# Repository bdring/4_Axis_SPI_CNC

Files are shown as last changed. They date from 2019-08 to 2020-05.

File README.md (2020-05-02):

# A 4 axis ESP32 CNC controller for daisy chained SPI stepper drivers.

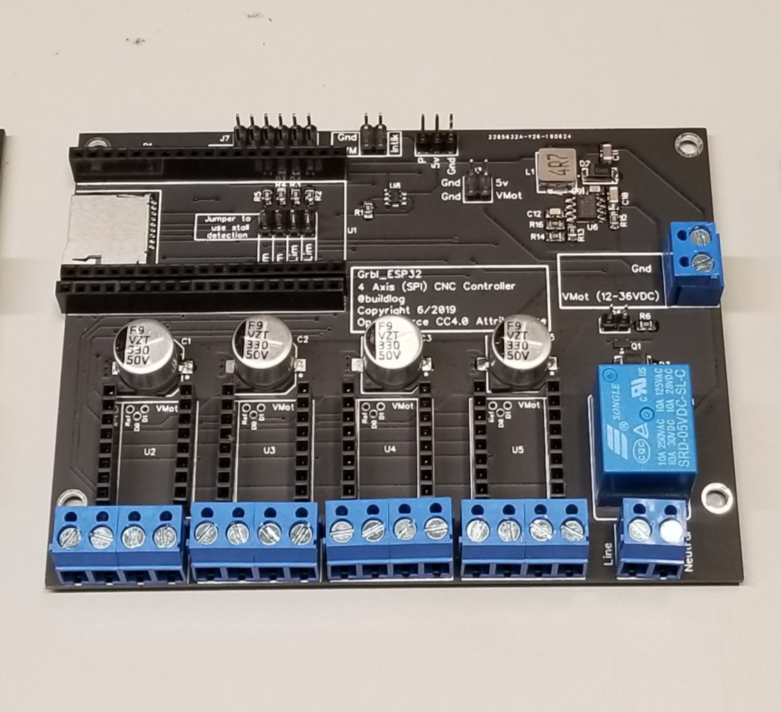
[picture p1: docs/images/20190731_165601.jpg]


### Trinamic Drivers

[Trinamic SPI stepper motor drivers](https://www.trinamic.com/products/integrated-circuits/) are great. They have dozens of features not found on traditional small stepper drivers. You can't control all the features via configuration pins, like the MS1, MS2 and MS3 traditionally used to select microstepping. They use SPI to setup and control the features. 

**Note:** Some of these drivers are sold in a pre-configured mode. They are often call "Stand Alone" versions of the drivers. This project is not compatible with those. It only works with SPI controlled drivers.

### About SPI Daisy Chaining

Typically each SPI device requires a SS (slave select) signal. With multiple drivers, this can cause problems with I/O pin count limited controllers, like the ESP32.

Most SPI devices can be used in a daisy chain mode (see image). As bits are received into a register via the MOSI pin,  bits are shifted out of the register of the MISO pin. Trinamic drivers use a a 40 bit wide register. To write to all three drivers shown below, you would send (3) sets of 40 bits. The first set of 40 bits would end up in the last driver. The SS line is pulled low once all drivers have their data. To write to only one driver, dummy data would be sent to the non targeted drivers. 



There is a very comprehensive and easy to use library, [TMCStepper](https://github.com/teemuatlut/TMCStepper), for SPI control, but it does not support daisy chaining. I created a fork that has a basic ability to write to any driver in an SPI daisy chain. It does not support reading data yet.

### Notes about the controller

- The SD card and drivers share the same SPI data lines. There is one SS for the SD and one SS for all of the drivers. 
- If you use less than (4) drivers, you need to jumper MOSI to MISO on the missing drivers to close the daisy chain loop.
- You can connect the DIAG1 pin of the drivers to the limit switches using jumpers JP1-JP4. Be sure to remove only one type of limit switch at a time.
- Source files
  - [Schematic (PDF)](https://github.com/bdring/4_Axis_SPI_CNC/blob/master/docs/1p3/SPI_4Axis_V1p3_Schm.pdf)
  - [Source Files (DipTrace)](https://github.com/bdring/4_Axis_SPI_CNC/tree/master/source/1p3/DipTrace)
  - [Gerbers](https://github.com/bdring/4_Axis_SPI_CNC/tree/master/source/1p3/Gerber)
  
### Plug In Modules

 - ESP32: The PCB uses ESP32 Dev Modules. It uses the 2 x 19 pin types with pin widths of either 0.9" or 1.0". 
 - Motor Drivers: It uses stepstick style stepper motor drivers with Trinamic SPI drivers. It has extra large capacitors.

### Firmware

- Use [Grbl_ESP32](https://github.com/bdring/Grbl_Esp32) with [spi_daisy_4axis.h](https://github.com/bdring/Grbl_Esp32/blob/master/Grbl_Esp32/Machines/spi_daisy_4axis.h) machine file

### I/O Expanders

Note: Obviously, external I/O expanders can be used increase I/O pin count. This project is focused on using only the I/O on the ESP32.

### Revision History

- **V1p2**
  - Added bypass jumper for 4th axis. Install jumper if 4th axis is not used. Normally the daisy chained SPI has to go through that axis.
  - Added 10uF optional capacitor to help with ESP32 modules that have trouble entering bootloader mode. This is not installed by default.
  - Added extra ground connection that TMC5160 drivers need. It is N/C on many other TMC drivers.

### Donation

This project represents a lot of work. Please consider a safe, secure and highly appreciated donation via the PayPal link below.



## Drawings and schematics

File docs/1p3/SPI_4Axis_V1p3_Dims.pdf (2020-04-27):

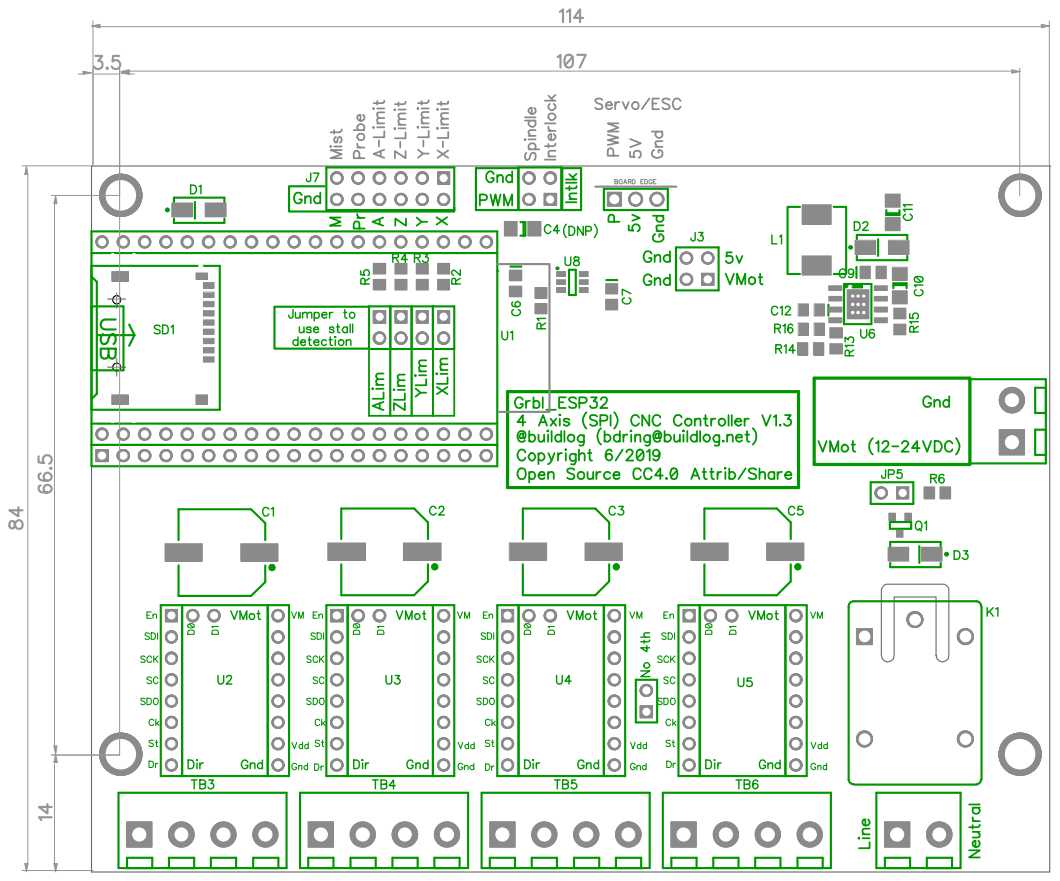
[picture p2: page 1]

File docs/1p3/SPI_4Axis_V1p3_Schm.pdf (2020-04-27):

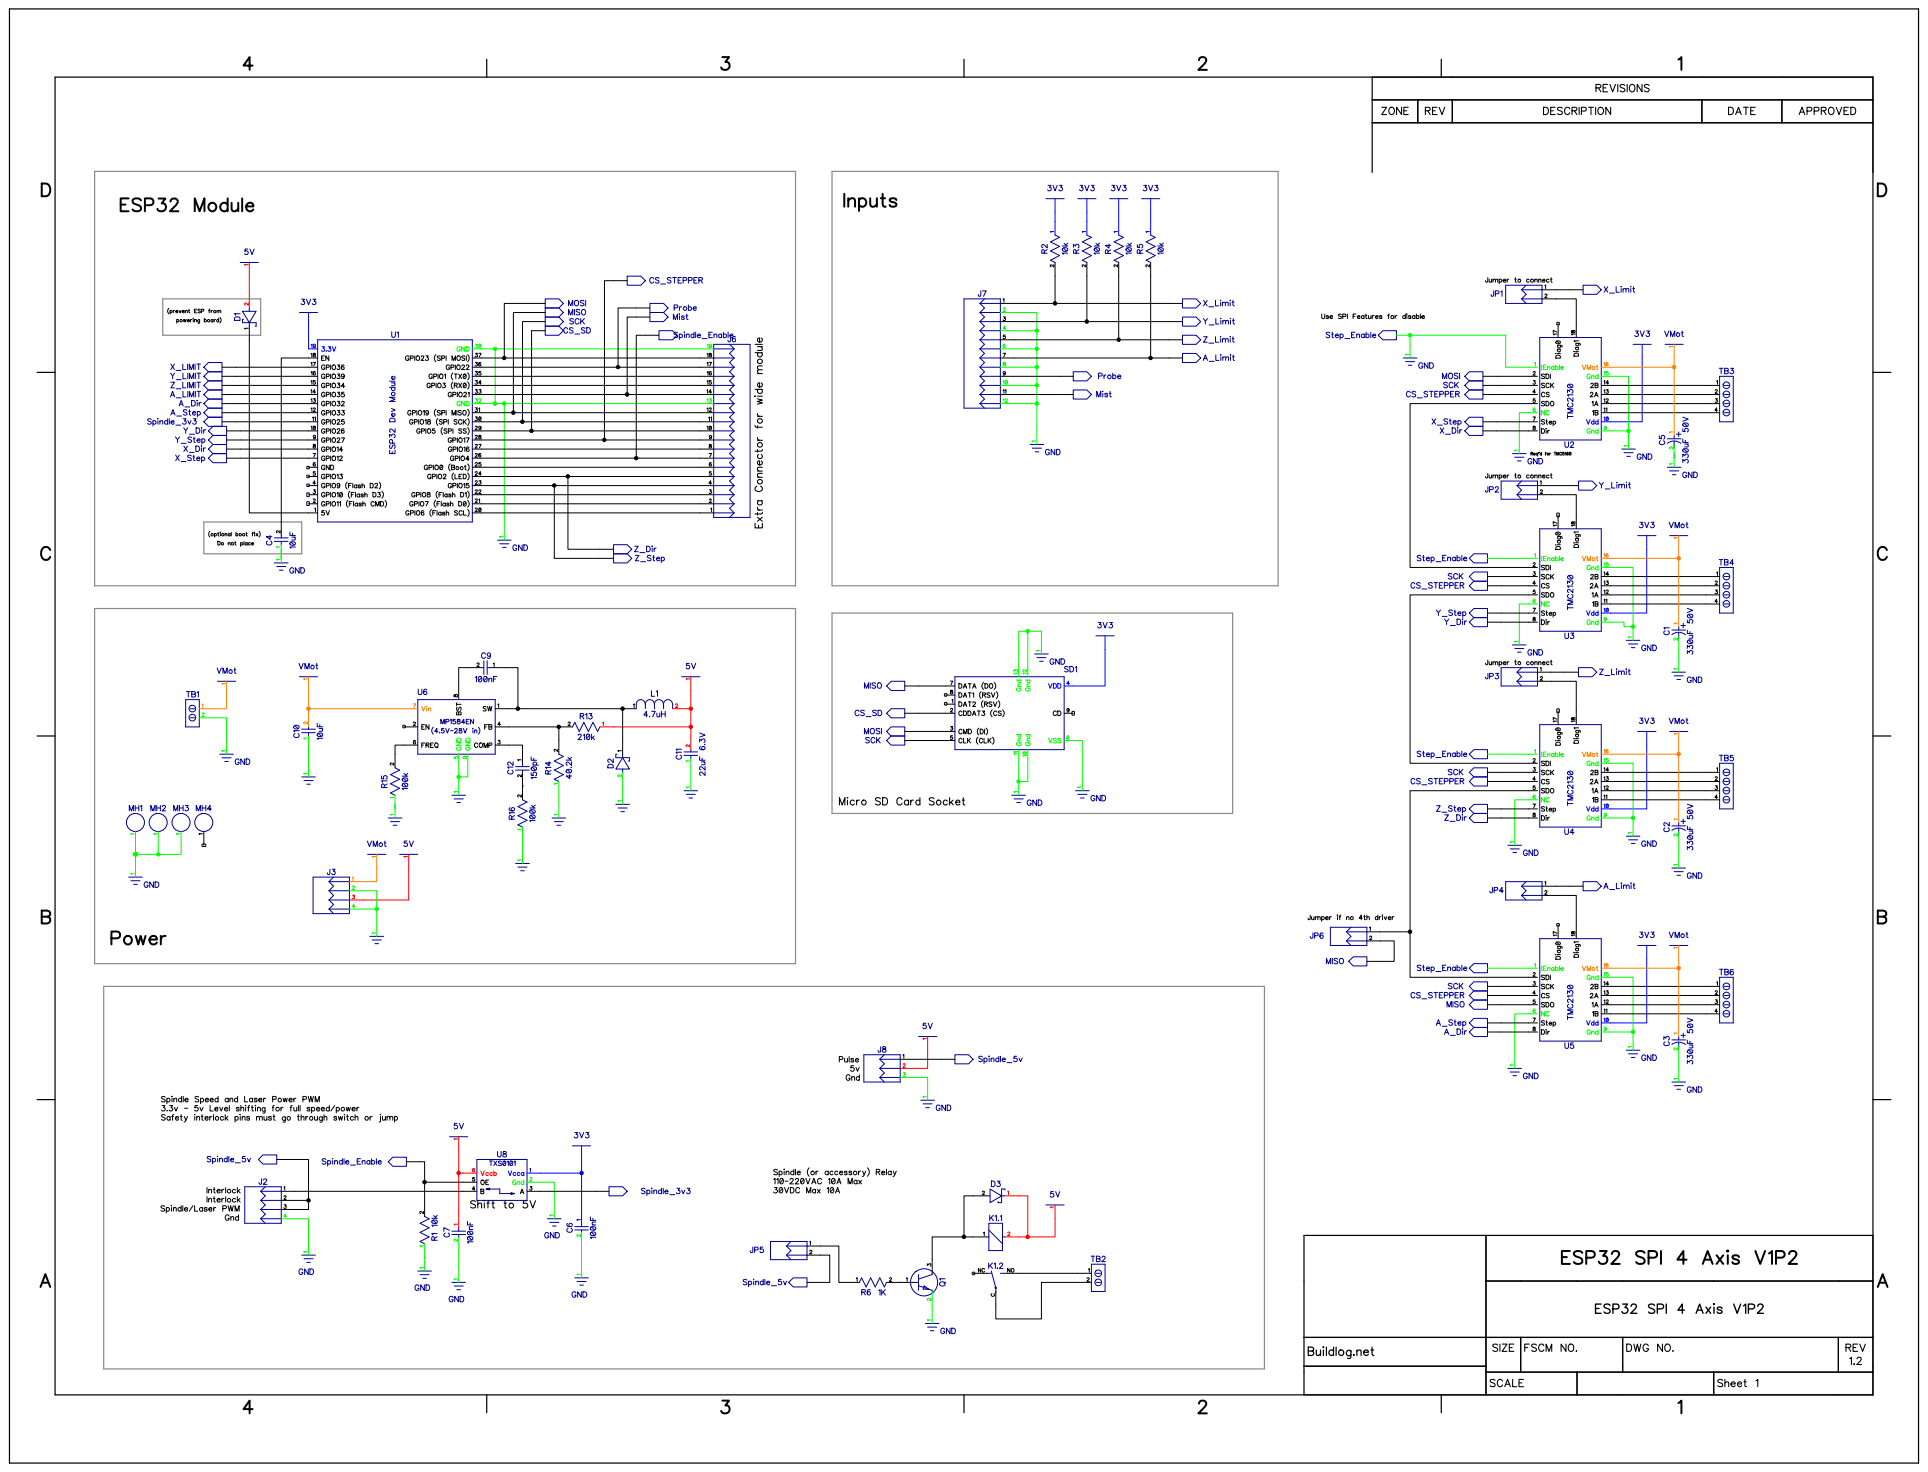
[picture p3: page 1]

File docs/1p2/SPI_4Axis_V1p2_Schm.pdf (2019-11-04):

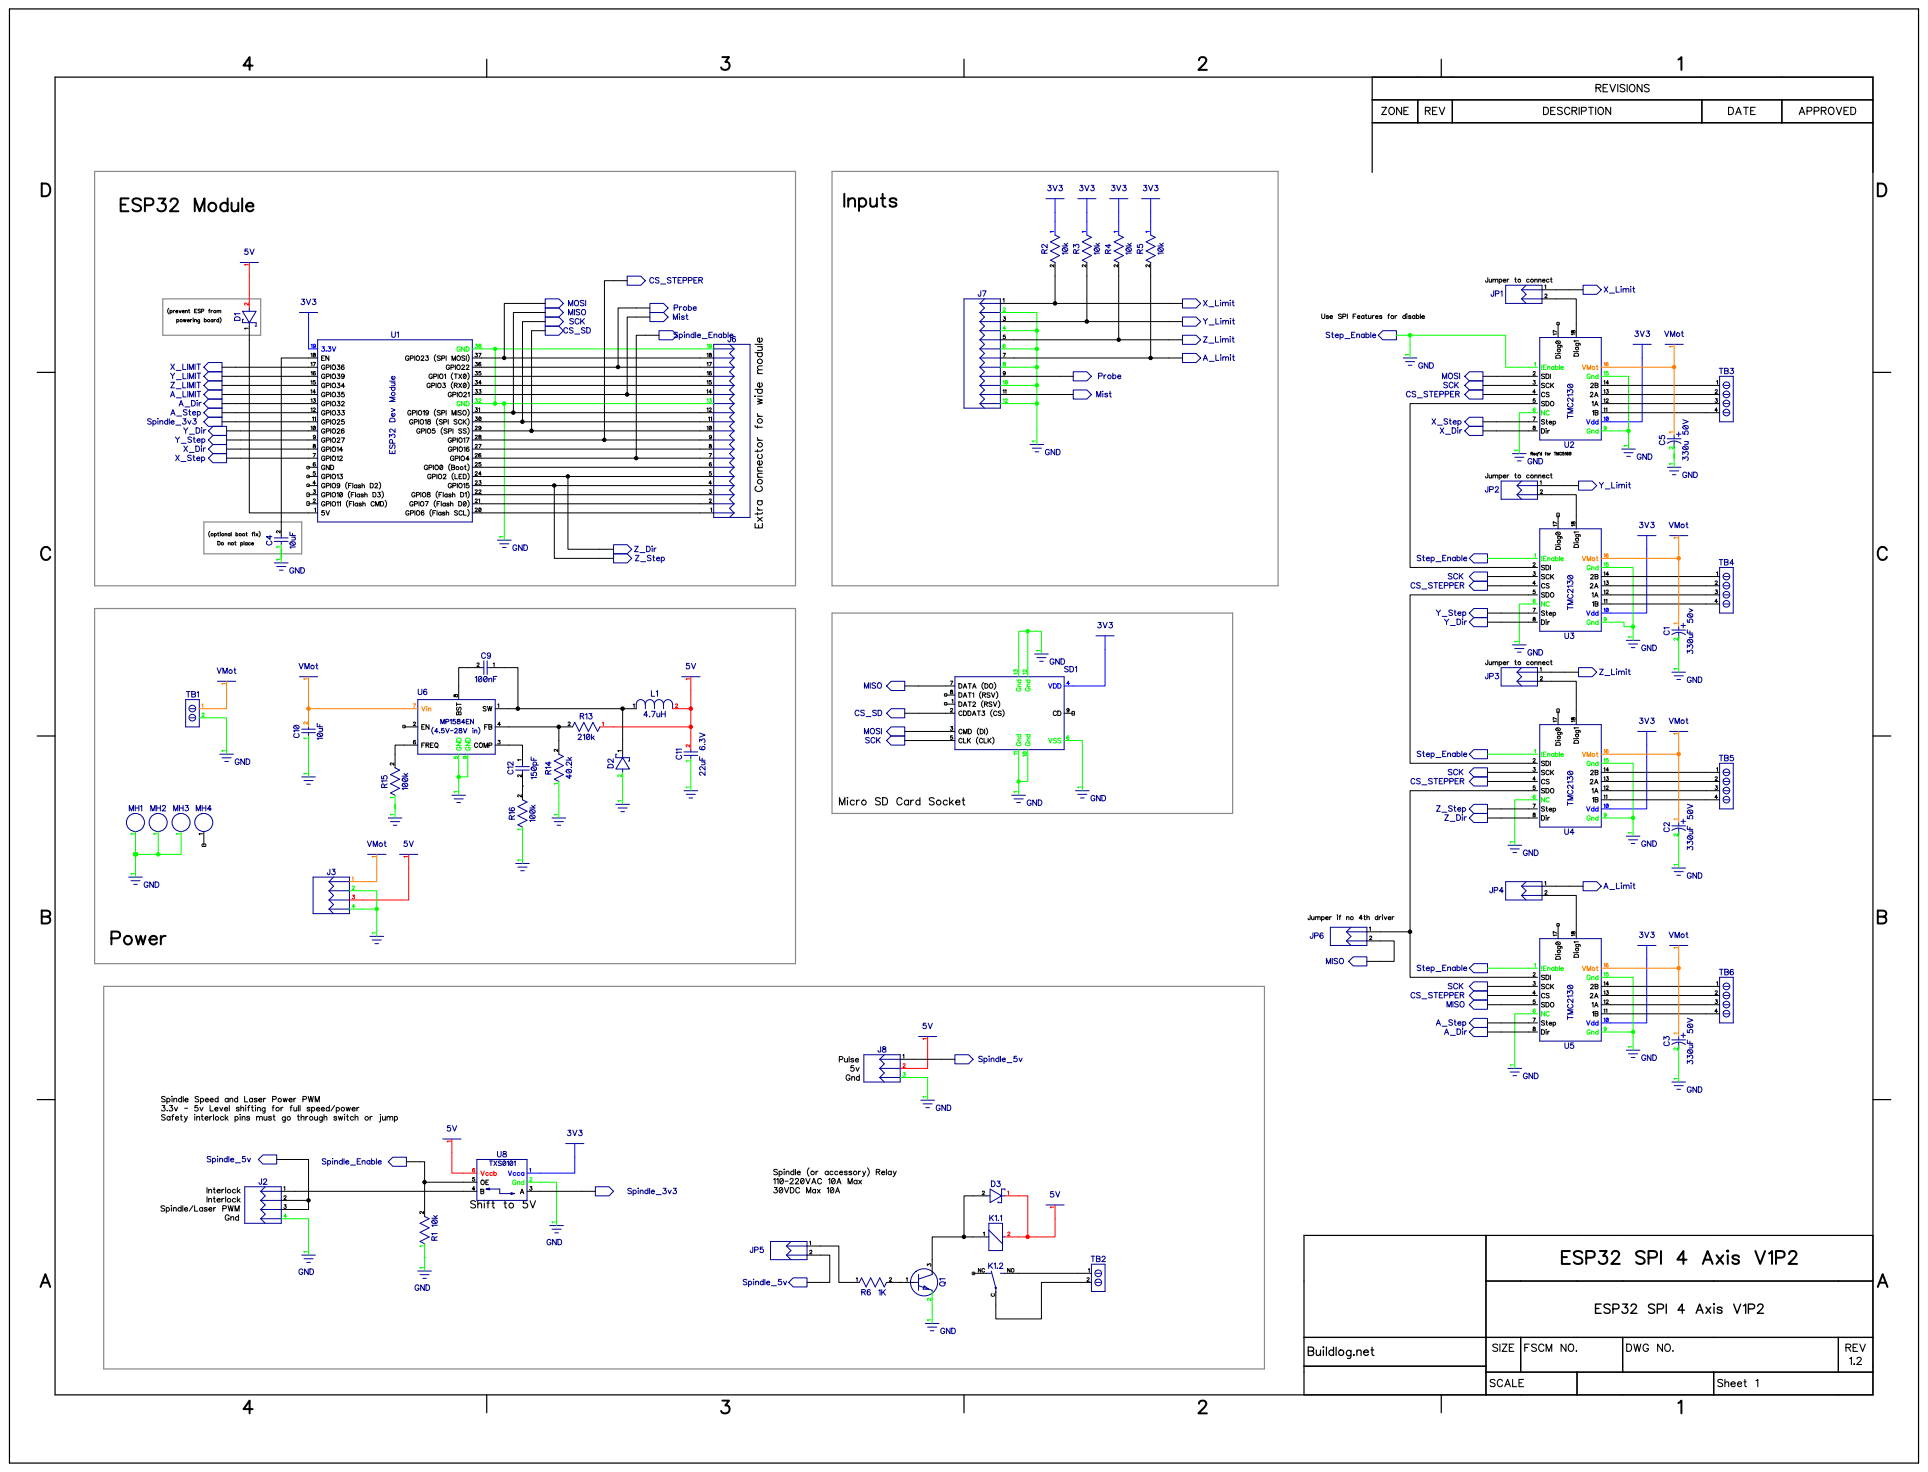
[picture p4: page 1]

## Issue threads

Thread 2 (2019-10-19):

where is cpu_map.h ?

cxandy, 2019-10-19:
thanks.

bdring, 2019-10-19:
This board used to require a fork of Grbl_ESP32 and a fork of TMCStepper.

The original TMCStepper has been updated to support daisy chained SPI and Grbl_ESP32 now uses that version. The old fork of Grbl_ESP32 was removed.

Support for daisy chained SPI can now be added to the master branch, but it has not been done yet. It is on my todo list, but behind a few other priorities. I hope to have it done by the end of the month.

shreeramlive, 2019-11-04:
In the schematic I noticed that the **Step/Dir** pins are physically connected to the ESP32 board. Do we need them for **SPI connection**, if they are not needed we can add some switches like Hold, Resume.
And the connection to the limit switches are without any **filter capacitors** unlike the [Grbl_ESP32](https://github.com/bdring/Grbl_ESP32_Development_Controller/blob/master/source/V3p5/schematic_esp32_cnc_test_v3p5.pdf) development board, are they necessary for the ESP32 boards?

bdring, 2019-11-04:
**Step/Dir** They are required. SPI primarily sets the features of the driver. It does have the ability to run motion profiles, but not step and direction. You could eliminate the driver **enable** pin. All the drivers share this one pin, but support would need to be added to Grbl for it.

**R/C filters on inputs** It is not typically required for smaller machines. Grbl also has debouncing that can be used. If you are using a larger machine with a high current spindle or laser, you might want to use them.

shreeramlive, 2019-11-09:
Hi, I have created a schematic with a slightly different pin map. **RC filters** are added for limit switches to be able to use with large machines.

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

[Schematic_esp32 grblcnc bk_Sheet_1 edit copy_20191109121537.pdf](https://github.com/bdring/4_Axis_SPI_CNC/files/3826991/Schematic_esp32.grblcnc.bk_Sheet_1.edit.copy_20191109121537.pdf)

A **TXS0104 level shifter** is also added to provide four 5V output pins to drive servo axes and spindle.
When spindle enable and coolant is not needed, can we use the `level shifter` pins as **inputs** for other functions like hold, resume?

I'm trying to create a prototype with this design, Do I have change any pin configuration?
Thanks

bdring, 2019-11-09:
As drawn, those are not R/C filters. There is no "R".

I suggest grounding the CLK pin on the drivers to make it compatible with TMC5160

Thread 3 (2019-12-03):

Connection issue with daisy chained TMC5160's

shreeramlive, 2019-12-03:
Hi I tried to connect 4 **TMC5160** in daisy chain. However I could not get the motor moving.  There seems to be a **SPI problem** with the TMC5160s. I have also _grounded_ the CLK pin

However I'm pretty sure that the boards works because when I connected the` A4988 drivers `it was working perfectly.
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
Here's the ESP32 connection diagram.

Is there any way to debug the TMC connection like in marlin (**M122**)?
I think there is a problem with the TMC5160 drivers, a fix for SKR1.3 was provided [here](https://github.com/teemuatlut/TMCStepper/pull/63/commits/c481cccf542f3243c2c0594f5cf765fde2dd22d0)
This was a patch for the SKR1.3 (LPC1768), Is there anything similar to get it working with the ESP32.
Thank you

BTW: This board is designed to support both standalone drivers and SPI drivers. That's how I was able to test the A4988 drivers

shreeramlive, 2019-12-03:
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

Here are some photos, Everything works well except the TMC5160 SPI connection.
P.S: Board named after the project creator @bdring.

bdring, 2019-12-03:
Can you provide the complete schematic, or at least the TMC5160 connections?

shreeramlive, 2019-12-03:
Yeah sure,
Most of the connections are similar to your 4 axis SPI board.

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

The extra headers are allow us to configure SD and SPI connections
Since I'm using TMC5160, I have grounded the CLK to ground

[sch2.0.pdf](https://github.com/bdring/4_Axis_SPI_CNC/files/3917623/sch2.0.pdf)

bdring, 2019-12-03:
What is the purpose of the stepper headers connected to 3.3V and CLK?

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

Try connecting CLK to ground.

shreeramlive, 2019-12-17:
**Thanks @bdring**, I have tried connecting the **CLK to ground**. Nevermind the headers in the schematic. Those extra headers are used to configure **Microsteps or SPI** connections with the help of **jumpers.**

Still no success with the TMC5160 stepsticks, I'm kind of confident that the _issue is with the TMC5160 drivers_. I have ordered some `TMC2130's` for testing. I will post updates when I receive them.

Is there any way to **debug** the `SPI connection` with the drivers?

Baramykin, 2020-12-24:
Hi,
I don't understand how to connect TMC5160 8 pcs to Teensy 4.1 in UART mode.
I can't find the schematics.
I want to use TMC5160 V1.2 drivers.
Help me if possible, please.

creatormir, 2021-05-11:
I've come to see the serial connection.
And about the SPI, I think the problem is the StepStick board. The SPI is blocked. We need to cut the track. That's where the https://github.com/bigtreetech/BIGTREETECH-TMC5160-V1.0/issues/8 discussed it.

The place to cut. It helped me.
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

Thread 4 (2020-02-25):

where to buy

haklein, 2020-02-25:
Hi @bdring,

would it be possible to buy one of the testing boards? I've some experience with TMCs from my Powder'o'matic project (https://github.com/haklein/Powder-O-Matic). I'd like to help with testing and convert a CNC controller (from an RS-CNC32) with external drivers to TMC5160.

br Hari

bdring, 2020-02-25:
I have a new version 1.3 that I plan to sell on Tindie soon. It will probably be at least 4-5 weeks before they are ready due to the problems in China.

I have 3 hand built prototypes that I would be happy to sell for $60 each. They would not include drivers or ESP32.

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

haklein, 2020-02-25:
I'd happily take one of these prototypes (I'd assume all features are tested and it's the same as the final version?).

bdring, 2020-02-25:
The design is 100% tested. Also, some new features have been added to Grbl_ESP32 to allow any these axes to be combined (2 motor on one axis).

Please sent $60 + $5 US shipping or $14 International to the PayPal donation link on the first page of this repo. Be sure to add a note about reason for the donation and include the shipping address. It will ship before the end of the week.

PolSerg, 2020-02-25:
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

Hello! And what is the difference from version 1.2, were there errors? I have already made a 1.2 board for myself, but have not yet soldered it, do I need to fix something to make it work?

bdring, 2020-02-25:
There is very little change between 1.2 and 1.3. 1.2 should work fine. These days there is very little additional cost to making changes between orders.

I think the input voltage range is mis-labeled on the 1.2. Max voltage should be 24VDC. The limiting factor for the input voltage is the 5V power supply.

haklein, 2020-02-28:
@bdring do I need a special branch of Grbl_ESP32 to run this board with TMC5160 and SPI? Or has this been integrated in master?

haklein, 2020-02-28:
pls ignore my last comment, I found  CPU_MAP_SPI_DAISY_4X in the map on master

haklein, 2020-03-25:
I'm very impressed with your board. Also with your code. Thanks a lot! The steppers work fine on my 3 axes, but I'm unable to trigger the relay. The interlock jumper is set (connecting the both interlock pins). The JP5 close to the relay is also bridged.
One of the Relay pins seems to not be soldered. Is this intentional?

bdring, 2020-03-25:
All pins should be soldered.

Your settings are correct.

haklein, 2020-03-25:
I've soldered the pin but the relay is still not working. I've verified GPIO 25 (Spindle_3v3) with a multimeter, and it toggles from 0 to 3.3V when being turned on via M3. But that's not arriving as 5V signal at the interlock.

haklein, 2020-03-25:
Applying 5V to JP5 operates the relay, so apparently there is an issue with the TXS0101. From the datasheets, the voltages at the pins should be fine. But I'm unsure about the orientation of the package, mind to cross check?
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

bdring, 2020-03-25:
That orientation is correct. do you have both jumpers installed?

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

haklein, 2020-03-25:
Yes, I have both jumpers connected as shown in your picture. I just had removed the interlock when taking the picture as I was also measuring on those pins.

bdring, 2020-03-26:
Remove the jumpers and measure the voltage with spindle on at GPIO_NUM_25, GPIO_NUM_4 and the  inner side of the interlock jumper.

haklein, 2020-03-26:
With both jumpers removed, when spindle is on, I get the following readings:
G25: 3,18V
G4: 3,17V
Inner side (closer to C4 pad) Interlock: 0,002V

bdring, 2020-03-26:
Measure the the voltage on the J3 5V pin.

On Thu, Mar 26, 2020 at 10:23 AM Harald Klein <notifications@github.com>
wrote:

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

--
Bart Dring

"If you did not build it, you will never own it"

haklein, 2020-03-26:
J3 5V shows 4,95V

bdring, 2020-03-26:
It seems like the level shifter is not working.  If you are just using the spindle, you could try to bypass the level shifter. The relay will work on 3.3V.

haklein, 2020-03-26:
Ok, thanks for the hint, I will try that. Can you tell me the exact part number for the shifter (same package/footprint etc), then I'll attempt to replace it.

bdring, 2020-03-26:
Texas Instriments TXS0101

haklein, 2020-03-26:
the TXS0101DBV as SOT-23 (6)?

bdring, 2020-03-26:
Yes.

If you want to bypass it, just remove it and bridge these 2 pins.

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

haklein, 2020-03-27:
I've connected GPIO25 to the right pin of JP5 with a wire, relay works with G3/G5 now. That will do fine until the TXS0101DBV arrives. Thanks for the hint.

haklein, 2020-04-16:
The replacement TXS0101DBV did arrive today. After replacement, the relay did still not work. In the end it was the solder joints of R1, apparently one was cold. Re-heating made the relay work. Thanks for your support and the nice board.

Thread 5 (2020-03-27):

[RFE] serial header

haklein, 2020-03-27:
It would be nice to have the serial pins accessible on a 4-pin header (RX, TX, GND, 5V). That would allow to easily connect a controller like: https://github.com/mstrens/grbl_controller_esp32

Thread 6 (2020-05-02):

Schematics link broken

VincentFrangi, 2020-05-02:
Hello,

The link to the schematics.pdf and some other links of README.md file are broke.
Thank you

bdring, 2020-05-02:
Thanks...fixed

Closed 2020-05-02.

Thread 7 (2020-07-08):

BOM anywhere?

gitxmax, 2020-07-08:
I'm far from US, so ordering the pre-made board is next to impossible.
Uploaded the gerber to Jlcpcb and found they can do SMT.
The problem is I went through every corner of this repository but failed to find the components list.
Any hint?
Thank you!

bdring, 2020-07-08:
Here is a PDF.

Note: JLCPCB has a very restrictive list of parts. I have never been able to use their service.

[SPI_4X V1.3 BOM.pdf](https://github.com/bdring/4_Axis_SPI_CNC/files/4892292/SPI_4X.V1.3.BOM.pdf)

gitxmax, 2020-07-10:
Thank you.
Went throgh the BOM, seems the following 2 components, might be a bit hard to get for me:

TXS0101DBVR - Level shifter
MMBT9013H - Transistor

Can this be replaced with something similar?

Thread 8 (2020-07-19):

Will this work with the TMC2208 V3

DrJohnM61, 2020-07-19:
First I just wanted to say that this is a fantastic initiative. I am about to purchase.

The spi_daisy_4axis.h file does not exist. Should I just use spi_daisy_4axis_xyz.h?

I notice that the Grbl_ESP32 code supports TMC2130, TMC2209 and TMC5160. I happen to have a number of TMC2208v3 spare and wonder if they can also be used? Apart from max current output and senseless homing (which I do not think you use anyway) and heat output, the TMC2209 and 2208 should be interoperable?

However, grbl_trinamic.h only defines TMC2130_RSENSE_DEFAULT and TMC5160_RSENSE_DEFAULT (and not for the TMC2209). Is that an omission? The TMC2209 (and 08) have the same as the TMC2130 ( 0.11). Should I update grbl_trinamic.h to include (at least) a TMC2209 and update spi_daisy_4axis_xyz.h to reflect the use of the different stepper?

Further, I get a warning on compiling stating "WARNING: library TMCStepper claims to run on avr architecture(s) and may be incompatible with your current board which runs on esp32 architecture(s)." - is this an issue or do I have to set some switch in the code to ensure compatibility?

Thank you in advance

DrJohnM61, 2020-08-20:
I went with TMC2130 so this is a non issue now.

Closed 2020-08-20.

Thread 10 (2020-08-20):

SD card not recognised

DrJohnM61, 2020-08-20:
I have tried plugging in an SD card (128mb) and tried a number of different formats (FAT12 and FAT), however, the ESP_32 web interface reports that there is no SD card. Is there a trick to getting the SD card to be recognised (I checked the code and the SD card option is tuned on). Does there are need to be in some other format (eg EXT)?

DrJohnM61, 2020-08-20:
By way of an update, the actual message in the web interface is "No SD Card". I also just tried the sd card formatted as ext4 without any joy.

bdring, 2020-08-20:
The wiki has some suggestions.

https://github.com/bdring/Grbl_Esp32/wiki/Using-the-SD-Card#card-formatting

DrJohnM61, 2020-08-20:
> The wiki has some suggestions.
>
> https://github.com/bdring/Grbl_Esp32/wiki/Using-the-SD-Card#card-formatting

Thank for directing me to that page. I am running on a Mac and also Raspberry pi, so that formatting solution did not work. I swapped out the card for a different one and that is recognised. On the basis that the no-working card is 128mb (yes mb, not gb), I suspect that it may be that the ESP-32 just does not like the card that is probably quite old.

Anyway - seems like I have a solution... Thanks for your help.

Closed 2020-08-20.

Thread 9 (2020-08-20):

Z Probe

DrJohnM61, 2020-08-20:
I have connected a basic touch contact to the probe connector but this does not work. I notice that the X/Y/Z/A limit switches have a 10k pull up resistor. Is this also required (to be added) for the probe pins or do I need some other type of probe?

If connecting a 10k resistor, what advice do you have as to where to connect that.

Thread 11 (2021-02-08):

VMOT voltage range clarification

red13dotnet, 2021-02-08:
Hi, I picked up one of your 1.3 boards last year and am just now getting to installation.  I'm doing a conversion on a 3040 engraver and the power output from the gutted control box that will be feeding VMOT is 27V.  I believe that is within spec for your buck converter and for my 5160 stepper drivers but the silkscreen lists 12v-24 volt for VMOT.  Just want to confirm this should be alright before I let the smoke out.

haklein, 2023-02-17:
@red13dotnet did it work for you with 27V VMOT?

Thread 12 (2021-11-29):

FluidNC config

haklein, 2021-11-29:
Is there a ready-to-use example config for this board in FluidNC?

jamhot1, 2022-03-26:
Me also. I am trying the standard 4axis config in the fluidnc example and can't get a motor to spin. I've used grbl for a while and this config file concept is confusing me a little.

boucz, 2022-03-26:
here is my config file, 3 axes (jumper shorting the fourth driver), tmc5160
`board: 4 Axis SPI Daisy
name: 4 Axis SPI Daisy

arc_tolerance_mm: 0.002

stepping:
  engine: RMT
  idle_ms: 255
  pulse_us: 4
  dir_delay_us: 1
  disable_delay_us: 0

axes:
  shared_stepper_disable_pin: NO_PIN
  x:
    steps_per_mm: 800.000
    max_rate_mm_per_min: 1500.000
    acceleration_mm_per_sec2: 80.000
    max_travel_mm: 500.000
    soft_limits: false
    homing:
      cycle: 2
      positive_direction: false
      mpos_mm: 0.000
      feed_mm_per_min: 200.000
      seek_mm_per_min: 200.000
      settle_ms: 500
      seek_scaler: 1.100
      feed_scaler: 1.100
      allow_single_axis: true

    motor0:
      limit_neg_pin: NO_PIN
      limit_pos_pin: NO_PIN
      limit_all_pin: gpio.36:low
      hard_limits: false
      pulloff_mm:1.000
      tmc_5160:
        cs_pin: gpio.17
        spi_index: 1
        r_sense_ohms: 0.075
        run_amps: 2.000
        hold_amps: 0.500
        microsteps: 16
        stallguard: 4
        stallguard_debug: false
        toff_disable: 0
        toff_stealthchop: 3
        toff_coolstep: 3
        run_mode: CoolStep
        homing_mode: Stallguard
        use_enable: false
        step_pin: gpio.12
        direction_pin: gpio.14
        disable_pin: NO_PIN

  y:
    steps_per_mm: 800.000
    max_rate_mm_per_min: 900.000
    acceleration_mm_per_sec2: 80.000
    max_travel_mm: 600.000
    soft_limits: false
    homing:
      cycle: 2
      positive_direction: false
      mpos_mm: 600.000
      feed_mm_per_min: 200.000
      seek_mm_per_min: 200.000
      seek_scaler: 1.100
      feed_scaler: 1.100
      allow_single_axis: true

    motor0:
      limit_neg_pin: NO_PIN
      limit_pos_pin: NO_PIN
      limit_all_pin: gpio.39:low
      hard_limits: false
      pulloff_mm:1.000
      tmc_5160:
        spi_index: 2
        r_sense_ohms: 0.075
        run_amps: 1.200
        hold_amps: 0.500
        microsteps: 16
        stallguard: 15
        stallguard_debug: false
        toff_disable: 0
        toff_stealthchop: 3
        toff_coolstep: 3
        run_mode: CoolStep
        homing_mode: Stallguard
        use_enable: false
        step_pin: gpio.27
        direction_pin: gpio.26
        disable_pin: NO_PIN

  z:
    steps_per_mm: 800.000
    max_rate_mm_per_min: 700.000
    acceleration_mm_per_sec2: 50.000
    max_travel_mm: 300.000
    soft_limits: false
    homing:
      cycle: 1
      positive_direction: true
      mpos_mm: 300.000
      feed_mm_per_min: 100.000
      seek_mm_per_min: 100.000
      seek_scaler: 1.100
      feed_scaler: 1.100
      allow_single_axis: true

    motor0:
      limit_neg_pin: NO_PIN
      limit_pos_pin: NO_PIN
      limit_all_pin: gpio.34:low
      hard_limits: false
      pulloff_mm:1.000
      tmc_5160:
        spi_index: 3
        r_sense_ohms: 0.075
        run_amps: 1.200
        hold_amps: 1.000
        microsteps: 16
        stallguard: 15
        stallguard_debug: false
        toff_disable: 0
        toff_stealthchop: 3
        toff_coolstep: 3
        run_mode: CoolStep
        homing_mode: Stallguard
        use_enable: false
        step_pin: gpio.15
        direction_pin: gpio.2
        disable_pin: NO_PIN

spi:
  miso_pin: gpio.19
  mosi_pin: gpio.23
  sck_pin: gpio.18

sdcard:
  card_detect_pin: NO_PIN
  cs_pin: NO_PIN

probe:
  pin: gpio.35:low
  check_mode_start: true

macros:
  startup_line0:
  startup_line1:
  macro0:
  macro1:
  macro2:
  macro3:

start:
  must_home: false

PWM:
  pwm_hz: 5000
  output_pin: gpio.25
  enable_pin: gpio.4
  direction_pin: NO_PIN
  disable_with_s0: false
  s0_with_disable: true
  spinup_ms: 0
  spindown_ms: 0
  tool_num: 0
  speed_map: 0=0% 12000=100%
`

jamhot1, 2022-03-26:
Thanks! Much appreciated! I'll be using the 2109 drivers in my build. Will this be compatible? Once I've got some motion I can start to experiment with the settings.
Thanks again

boucz, 2022-03-26:
Do you mean TMC2209? If so, you'll have a problem as on this board ESP32 uses SPI to speak to drivers (TMC2130, TMC5160 compatible). TMC2209 are serial drivers, you'll need a different board to use them.

jamhot1, 2022-03-27:
Yes. The tmc2209. Damn I cancelled my order for the 2130 in favour of these. I'll get some 5160's. At least it will be a clone of your current setup and I can start to figure the rest out. Thanks again for the pointers.
Ps, when you say serial. Is that described as UART. In the product description?

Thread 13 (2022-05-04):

Alternative to MP1584EN-LF-Z for input 50V

alfredanil, 2022-05-04:
Is there an alternative to MP1584EN-LF-Z, as it has a limited input voltage of 28V. I plan to run stepper motors at 48V.

bdring, 2022-05-04:
I have been using the TI TPS54360DDAR. It is good to 60V. I have it on this circuit.

https://oshwlab.com/bdring/tmc2130-2-axis.

Open sheet 1 to see the circuit.

alfredanil, 2022-05-05:
> TI TPS54360DDAR

Can it (TPS54360DDAR) be replaced directly without any changes to the current design with MP1584EN-LF-Z ?

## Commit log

2019-08-12 Adding files
    [BoardOutline.gbr, Bottom.gbr, BottomMask.gbr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]
2019-11-04 Added Version 1p2
    Rearranged folders to show versions. See readme for version info
    [BoardOutline.gbr, Bottom.gbr, BottomMask.gbr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]
2020-04-27 Re-arranged files and added V1p3
    [BoardOutline.gbr, Bottom.gbr, BottomMask.gbr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]
